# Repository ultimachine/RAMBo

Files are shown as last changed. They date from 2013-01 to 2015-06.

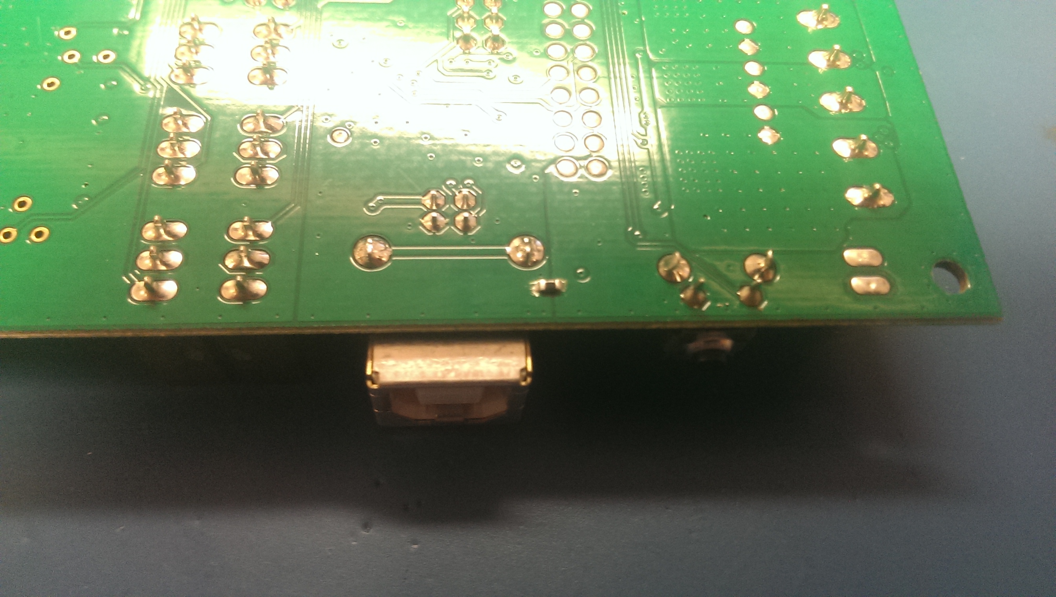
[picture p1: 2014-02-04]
docs/v1-2-ESD-patch/SMT-patch.jpg

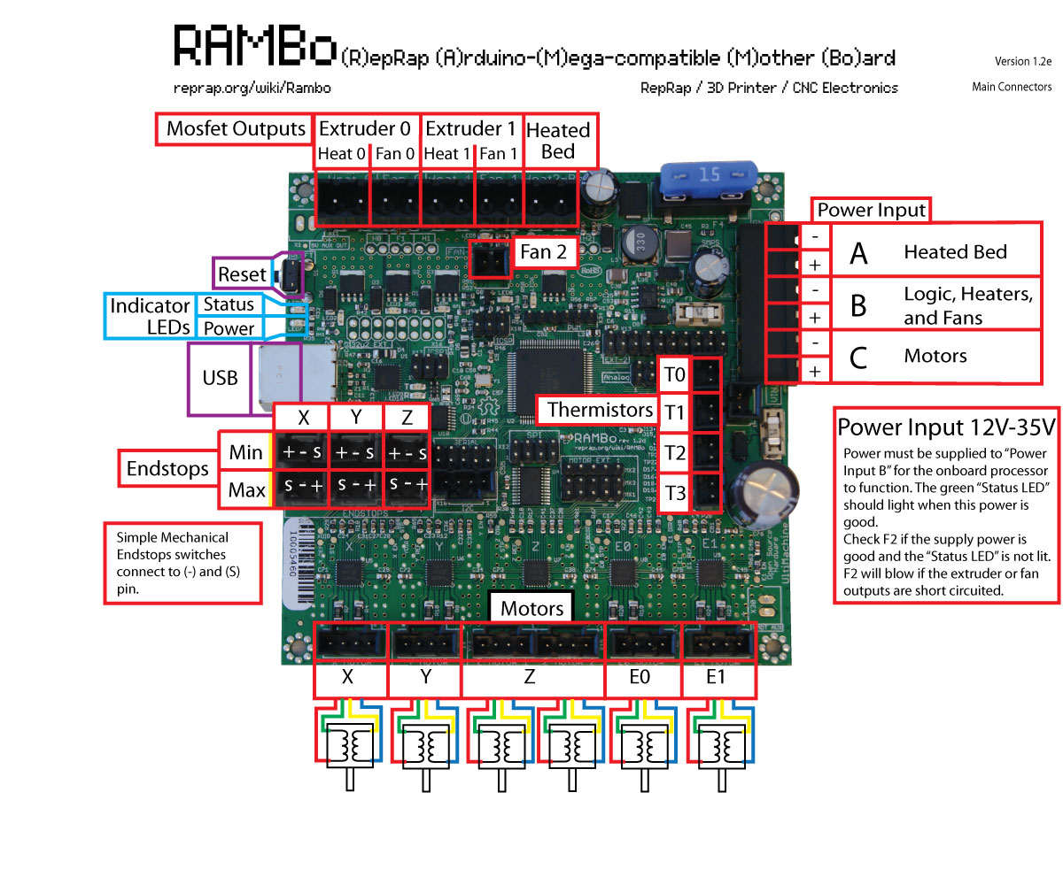
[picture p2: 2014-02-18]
docs/images/Rambo-conn-main.jpg

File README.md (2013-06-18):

RAMBo 3D Printer electronics
=====

This board is based off the Arduino MEGA design and work of RepRap community. It has 5 stepper drivers and 5 mosfet switched outputs.

There is no warantee for these files in any way. They are used to produce these boards, but there may have been some undocumented tweaks by various designers, engineers, manufacturers, suppliers, and assemblers to make this a functional product.

If you have any questions, suggestions, or comments please use the issues tracker at github.org/ultimachine/RAMBo/issues for now.

Please report bugs at github.org/ultimachine/RAMBo/issues

Documentation is at reprap.org/wiki/rambo

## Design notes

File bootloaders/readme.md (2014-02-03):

Use https://github.com/arduino/Arduino-stk500v2-bootloader for the Atmega2560 bootloader

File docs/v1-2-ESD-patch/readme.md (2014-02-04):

Applicable to RAMBo version 1.2

You should be able to get the patch from the vendor where you received the RAMBo.

The patch is a varistor between the USB ground and primary ground to provide a path for ESD to the USB shield.

The plug-in-patch uses part number VA100026D580DL between GND pins in ICSP1 and Serial extensions. If you are using the serial extension you can use GND in ICSP, I2C, or Z-MAX. The varistor should be completely covered in heat shrink tubing.

The SMT patch uses part CG0603MLC-05E.

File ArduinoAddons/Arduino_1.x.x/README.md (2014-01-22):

To access the extra pins in EXT-2 header:  

Install the arduino software IDE/toolset 1.x.x http://www.arduino.cc/en/Main/Software  

Current recommended is Arduino version 1.0.5
The rambo directory here needs to be copied to the arduino environment in the hardware folder. You should end with a boards.txt file at arduino-1.0.5/hardware/rambo/boards.txt

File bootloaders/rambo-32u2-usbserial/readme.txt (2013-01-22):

//this firmware and document modified from Arduino's source.
To setup the project and upload the RAMBo usbserial application firmware to an ATMEGA32U2 using the USB DFU bootloader:
1. unpack the source into LUFA's Projects directory
2. set ARDUINO_MODEL_PID in the makefile as appropriate
3. do "make clean; make"
4. put the 8U2 into USB DFU mode:
4.a. assert and hold the 8U2's RESET line
4.b. assert and hold the 8U2's HWB line
4.c. release the 8U2's RESET line
4.d. release the 8U2's HWB line
5. confirm that the board enumerates as either "Arduino Uno DFU" or "Arduino Mega 2560 DFU"
6. do "make dfu" (OS X or Linux - dfu-programmer must be installed first) or "make flip" (Windows - Flip must be installed first) or use the AVR Flip app.

Check that the board enumerates as either "RAMBo". You may also need to upload stk500v2 bootloader to the 2560 if it is not already. 
Test by uploading a new Arduino sketch from the Arduino IDE.

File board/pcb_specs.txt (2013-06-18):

4 layers, 0.062", FR4-TG170, 2oz, ENIG GOLD, GREEN SOLDER MASK, TWO SIDE MASK, WHITE SILK SCREEN, TOP SILK, Min Trace: 6mil, 4.05" x 4.10"11

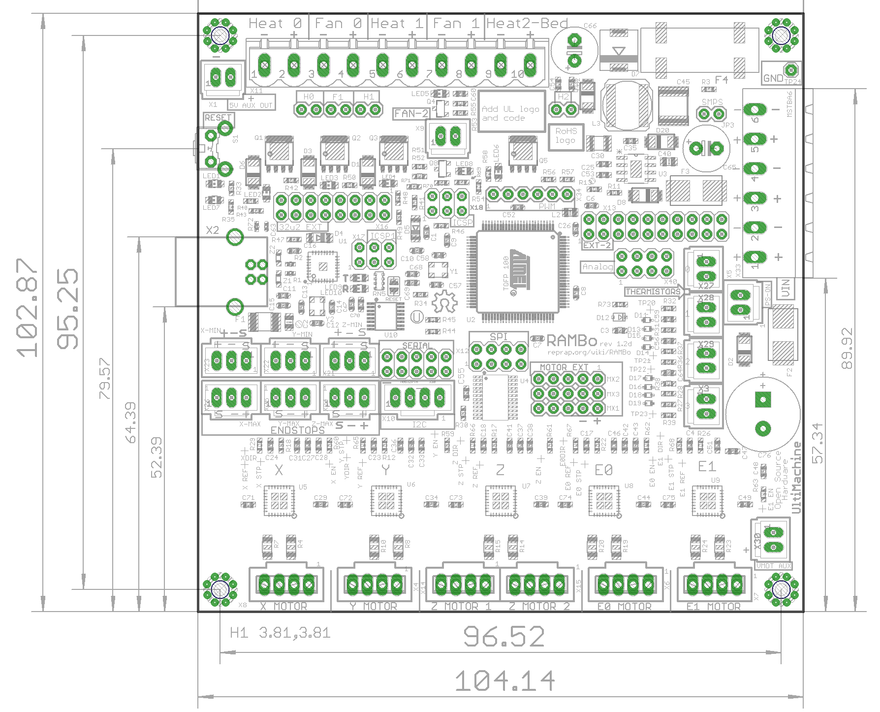
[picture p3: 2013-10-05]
docs/images/RAMBo-Silk.png

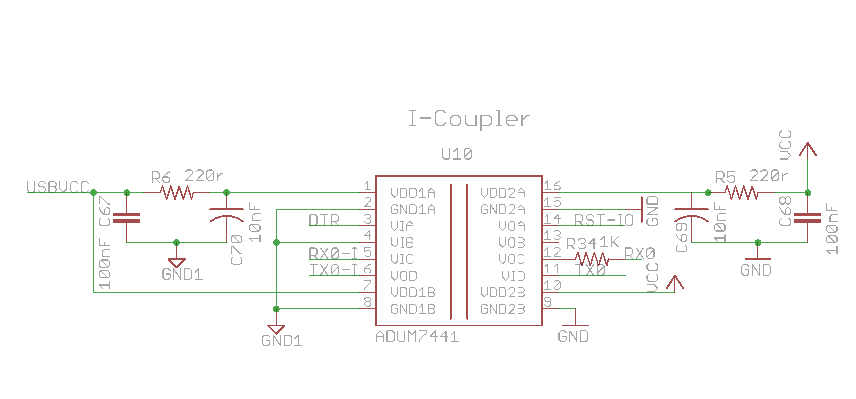
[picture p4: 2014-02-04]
docs/v1-2-ESD-patch/schem.png

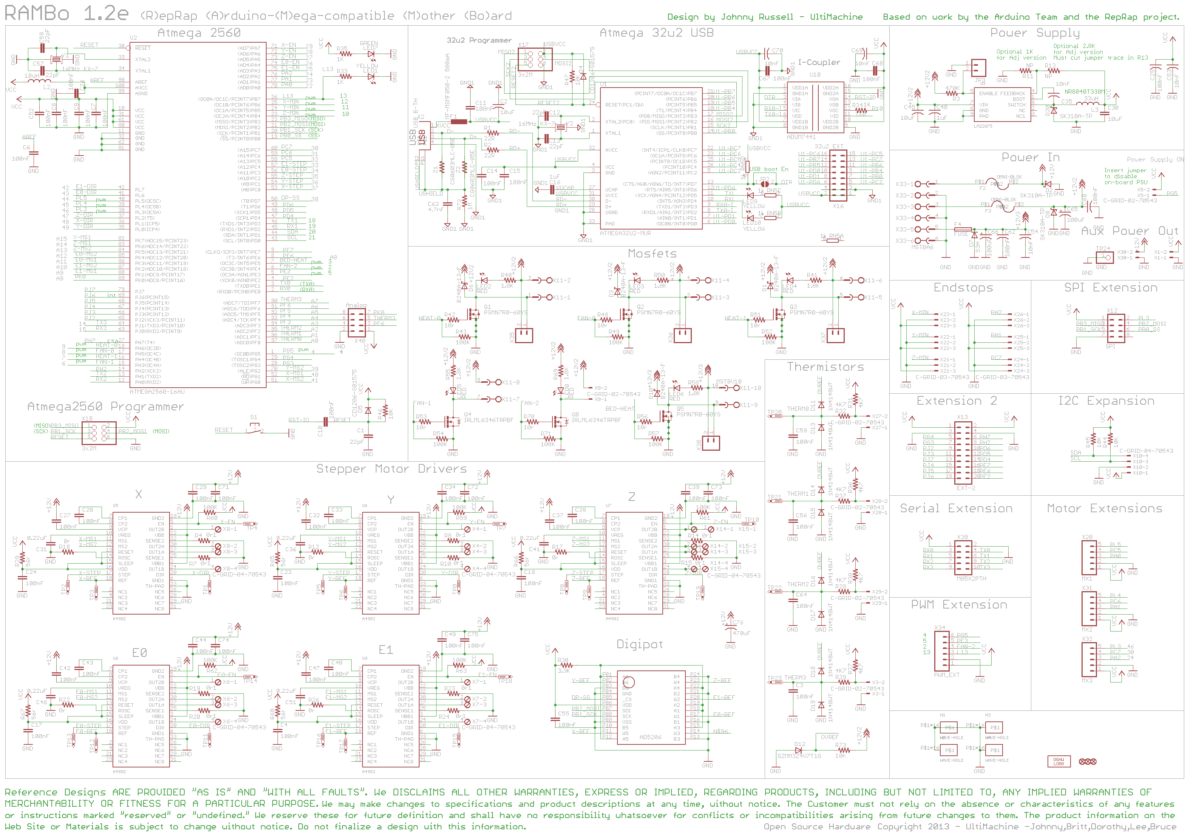
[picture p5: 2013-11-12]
docs/images/RAMBo-Schem.png

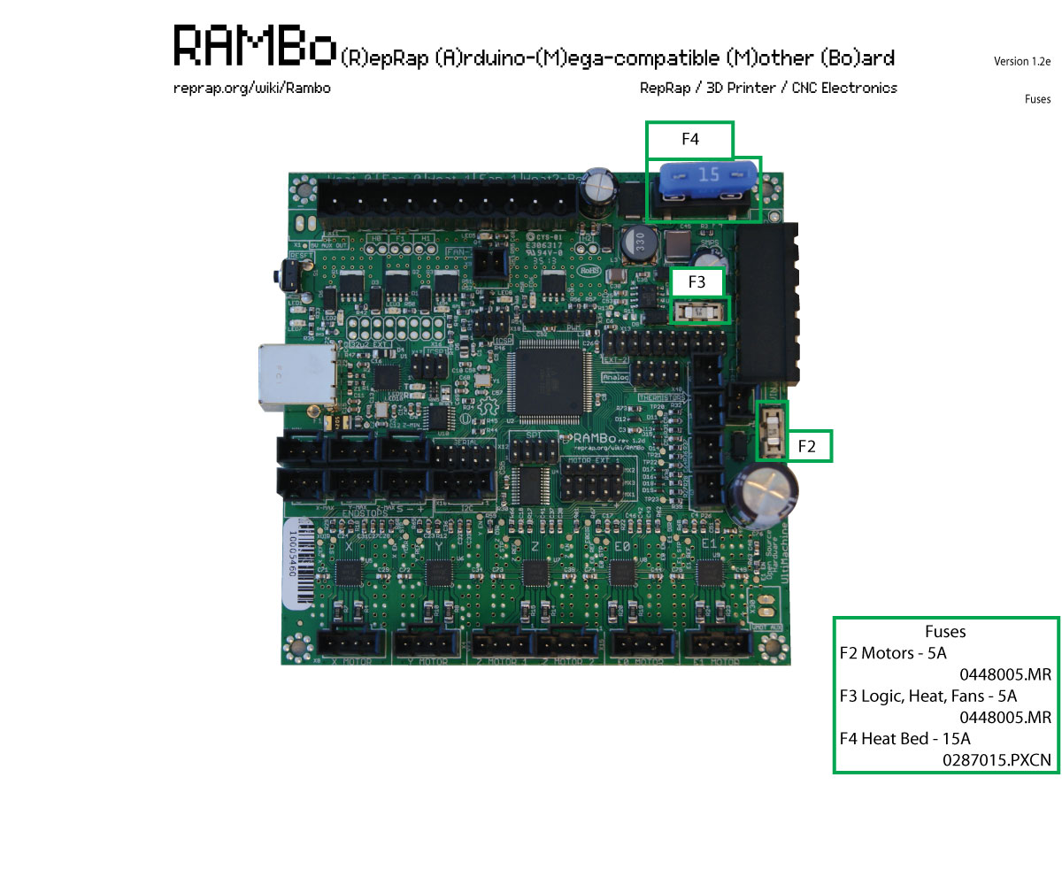
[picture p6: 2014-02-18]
docs/images/Rambo-fuses.jpg

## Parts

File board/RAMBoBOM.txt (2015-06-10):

Parts;Qty;Value;Device;Package;Description;Manufacturer;mfr  part #;;;
S1;1;;31-XX;B3F-31XX;SWITCH, TACTILE, SPST-NO, 50mA, THD ;Omron;1571610-2;;;
JP3, X35, X36, X37, X38;1;;M02PTH;1X02;1x2 header;;2211S-02G;;;
C31, C36, C41, C46, C51;5;0.22uF;C-EUC0603;C0603;0.22uF 100V capacitor X or 15%;Yageo;CC0603KRX7R7BB224 ;;;
R12, R17, R18, R22, R26;5;0r;R-US_R0603;R0603;0r (zero ohm) 100mW 5% resistor;Bourns;CR0603J000ELF;;;
R4, R7, R8, R10, R14, R15, R19, R20, R23, R24;10;0r1;R-US_R1206;R1206;0r1 (0.1ohm) .5mW 1% resistor;Bourns;CRM1206-FX-R100ELF;;;
R40, R41, R50, R55, R58, R69;6;1.8K;R-US_R0603;R0603;Resistor, Thick Film, 1.8K Ohm, 50V, 5±%, 100ppm, 0603 Case Size ;;RC0603JR-071K8L;;;
R43, R49, R52, R54, R57, R59, R60, R61, R62, R63, R71;11;100K;R-US_R0603;R0603;100Kohm 100mW 1% resistor;Yageo;RC0603FR-07100KL;;;
C6, C7, C8, C9, C10, C11, C14, C15, C26, C52, C3, C4, C17, C18, C23, C24, C27, C28, C29, C32, C33, C34, C37, C38, C39, C42, C43, C44, C47, C48, C49, C55, C56, C59, C64, C71, C72, C73, C74, C75, C25, C60, C62;43;100nF;C-EU0603-RND;C0603-ROUND;0.1uF 50V capacitor;Kemet;x16;;;
C65, C66;2;100uF;CPOL-USE3.5-8;E3,5-8;Aluminum Electrolytic Capacitors - Leaded 100uF 50V 20% 105c ;Nichicon;UVZ1H101MPD1TD;;;
R44, R45, R46, R47, R73;5;10K;R-US_R0603;R0603;10Kohm 100mW 1% resistor;Panasonic;ERJ-3EKF1002V;;;
C35, C53, C54;3;10nF;C-USC0603;C0603;10nF (0.01uF) 25V capacitor;TDK;C1608X7R1E103K080AA;;;
R42, R48, R51, R53, R56, R70;6;10r;R-US_R0603;R0603;10r (10ohm) 100mW 1% resistor;Vishay;CRCW060310R0FKEA;;;
C30;1;10uF;C-EUC1210K;C1210K;Multilayer Ceramic Capacitors MLCC - SMD/SMT 1210 10uF 25volts X5R 10% ;TDK;C3225X5R1E106K;;;
C2;1;10uF;C-USC0805;C0805;10uF;Kemet;C0805C106K8PACTU;;;
C45;1;10uF;C-USC2220K;C2220K;10uF;TDK;C5750X7R1H106M230KB;;;
Y1, Y2;2;16MHz KX-7;CRYSTAL-3.2-2.5;CRYSTAL-3.2-2.5;16MHz KX-7 10ppm crystal;TXC;7M-16.000MEEQ-T;;;
R33, R34, R35;3;1K;R-US_R0603;R0603;RESISTOR, THICK FILM, 1KOHM, 100mW, 1% ;Panasonic;ERJ-3EKF1001V;;;
R72;1;1M;R-US_R0402;R0402;RES 1M OHM 1/10W 5% 0402 SMD;Panasonic;ERJ2GEJ105X;;;
D11, D13, D14, D15, D16, D17, D18, D19;8;1N4148WT;1N4148WT;SOD523;Diode Small Signal Switching 75V 2-Pin SOD-523F T/R ;Fairchild;1N4148WT ;;;
RN5;1;1k;4R-NCAY16;CAY16;Resistor Networks & Arrays 1K 5% Convex 4resistors ;Bourns;CAY16-102J4LF;;;
C16;1;1uF;C-EU0603-RND;C0603-ROUND;1uF 10V capacitor;yageo;CC0603ZRY5V6BB105 ;;;
C40;1;1uF;C-USC0805;C0805;Multilayer Ceramic Capacitors MLCC - SMD/SMT 1.0UF 50V 10% 0805  ;Murata;GRM21BR71H105KA12L;;;
R1, R2;2;22R;R-US_R0402;R0402;22R (22ohm) 62.5mW 1% resistor;Yageo;RC0402FR-0722RL;;;
C1, C12, C13, C57, C58;5;22pF;C-EU0603-RND;C0603-ROUND;22pF 50V capacitor;TDK;C1608C0G1H220J;;;
R30;1;3.3K;R-US_R0603;R0603;RESISTOR, THICK FILM, 3.3KOHM, 100mW, 5% ;panasonic;erj3geyj332v;;;
X16;0;32u2 EXT;M08X2;2X8;2x8 header;;;;;
L3;1;33uH;L-USNR8040;NR8040;Fixed Inductors 33uH;TDK;VLP8040T-330M;;;
X17, X18;2;3x2M;PINHD-2X3;2X03;2x3 header;;2213S-06G;;;
C63;1;4.7nF;C-EUC0402;C0402;Multilayer Ceramic Capacitors MLCC - SMD/SMT 4.7nF 25V X7R 10% ;;CC0402KRX7R8BB472;;;
R3;1;470K;R-US_R0603;R0603;SMD 1/10watt 470Kohms 1% Thick Film Resistors;Vishay;CRCW0603470KFKEA ;;;
C76;1;470uF;CPOL-USC12,5-5;C12,5-5;CAPACITOR ALUM ELEC, 470UF, 50V, 20%, RADIAL;nichicon;UPW1H471MHD1TO;;;
;0;;;;Alternate capacitor;;UVZ1H471MHD1TO;;;
R27, R28, R31, R32, R36, R37, R38, R39;8;4K7;R-US_R0603;R0603;4K7 (4.7Kohm) 100mW 1% resistor;Panasonic;ERJ3EKF4701V;;;
R29, R65, R66, R67, R68;5;56r;R-US_R0603;R0603;RESISTOR, THICK FILM, 56OHM, 100mW, 5% ;Vishay;CRCW060356R0JNEA;Till 05/22/2014;200bds w/drivers;
U5, U6, U7, U8, U9;5;A4982;A4982QFN32ROUNDPADS;QFN32TROUND;A4982;Allegro;A4982SETTR-T;2100;6500;325
U4;1;AD5206;AD5206;TSSOP24;AD5206 (IC);Analog Devices;AD5206BRUZ10-RL7;;currently 300bd/wk;
U10;1;ADUM7441;ADUM7441;QSOP16;ADUM7441;Analog Devices;ADUM7441ARQZ-RL7;;;
U2;1;ATMEGA2560-16AU;ATMEGA25602560-16AU;TQFP100;ATMEGA2560-16AU (IC);Atmel;ATMEGA2560-16AUR;;;
U1;1;ATMEGA32U2-MUR;ATMEGA16U2-MU;MLF32;ATMEGA32U2-MUR (IC);Atmel;ATMEGA32U2MU;;;
D1, D3, D6, D10;7;B240A-13-F;SCHOTTKY-DIODE;SMA-SM;3.0A 100V Diode;Diodes Inc.;SK310A-TP;;;
X1, X3, X5, X9, X27, X28, X29, X30;6;C-GRID-02-70543;C-GRID-02-70543;70543-02;WIRE-BOARD CONNECTOR HEADER 2POS, 2.54MM ;Molex;70543-0001;;;
X21, X22, X23, X24, X25, X26;6;C-GRID-03-70543;C-GRID-03-70543;70543-03;WIRE-BOARD CONNECTOR HEADER 3POS, 2.54MM ;Molex;70543-0002;;;
X4, X6, X7, X8, X10, X14, X15;7;C-GRID-04-70543;MPT4;4POL254;WIRE-BOARD CONNECTOR HEADER 4POS, 2.54MM ;Molex;70543-0038;;;
L2;1;10uH;L-US;C0805;INDUCTOR 10UH 20% 0805 SMD;Taiyo Yuden;CBC2012T100M;;;
D4, D5;2;CD1206-S01575;DIODE-MINIMELF;MINIMELF;100V 150mA diode;Bourns;CD1206-S01575;;;
Z1, Z2;2;CG0603MLC-05E;VARISTORCN0603;CT/CN0603;5V 20V varistor;Bourns;CG0603MLC-05E;;;
X13;1;EXT-2;M10X2;2X10;2x10 header;;2213S-20G ;;;
F4;1;FUSE;FUSE;FUSE-ATO-SMD;FUSE HOLDER, AUTO BLADE, SMT ;Keystone;3587TR;;;
D40;1;RSB39VTE-17;PINHD-1X1;SOD323;TVS DIODE 30VWM SOD323;;RSB39VTE-17;;;
D9, D21, D22, D23, D24, D25, D26, D27, D28, D29, D30, D31, D32, D33, D34, D35, D36, D37, D38, D39;20;GND;PINHD-1X1;1X01;TVS DIODE 30VWM SMD ;;SMAJ30A;;;
C67, C68, C69, C70;4;100nF;C-EU0603-RND;C0402;CAP CER 0.1UF 16V 10% X7R 0402 ;;GRM155R71C104KA88D ;;;
LED7;1;GREEN;LEDCHIP-LED0805;CHIP-LED0805;GREEN LED;;598-8170-107F ;;;
Q4, Q8;2;IRLML6346TRPBF;MOSFET-NCHANNELSMD;SOT23-3;N CH MOSFET, 30V, 3.4A, 3-SOT-23;;IRLML6346TRPBF;;;
U3;1;LM22675;LM22675;SOIC127P600X170-9N;IC REG BUCK 5V 1A 8SOPWRPAD;;LM22675;;;
X20;1;M05PTH;M05PTH;1X05;1x5;;2211S-05G;;;
X39, X32;2;M05X2PTH;M05X2PTH;AVR_ICSP;2x5 header;;2213S-10G;;;
F1;1;MF-MSMF050-2 500mA;L-EUL1812;L1812;500mA 15V fuse ptc reset;Bourns;MF-MSMF050-2;;;
X33;1;MSTBA6;MSTBA6;MSTBA6;6 pin fixed terminal block;Molex;39532-1006;;;
X11;1;MSTBV10;MSTBV10;MSTBV10;CONN HEADER 10POS 5.08MM STR TIN;Molex;395311010;;;
R11, R13;0;NP;R-US_R0603;R0603;;;;;;
F2, F3;2;OMNI-BLOK;OMNI-BLOK;OMNI-BLOK;5A fuse/fuse block;Littlefuse;0154005.DR;;;
Q1, Q2, Q3, Q5;4;PSMN7R0-60YS;PH7030L;SOT669;PH7030L (Mosfet) 60V 356A 117W;NXP;PSMN7R0-60YS,115;;;
X34;1;PWM_EXT;M06SIP;1X06;1x6 header;;2213S-06G;;;
LED2, LED3, LED4, LED5, LED6, LED8;6;RED;LEDCHIP-LED0805;CHIP-LED0805;RED;Dialight;5988110107F ;;;
D7;1;S3A;DIODE-D0-214AB;DO-214AB;3A 50V Diode;;S3A;;;
X12, X40;2;SPI;M04X2;2X4;M04X2;;2213S-08G ;;;
D12;1;SZMM3Z4V7T1G;ZENER-DIODESOD323;SOD323-R;Zener Diodes ZEN REG 0.2W 4.7V;;SZMM3Z4V7T1G;;;
X2;1;USB B-TH;PN61729;PN61729;USB B-TH connector;FCI;61729-0010BLF;;;
LED1, LED9, LED10;3;YELLOW;LEDCHIP-LED0805;CHIP-LED0805;YELLOW LED;Dialight;    5988140107F;;;
CF1, CF2, CF3, CF4, CF5, CF6, CF7, CF8, CF9, CF10, CF11, CF12, CF13, CF14, CF15, CF16, CF17, CF18, CF19, CF20;20;;;;EMI Filter 2A 50VDC Flat Style SMD;;NFM21CC223R1H3D;;;
L1, L4;2;;;;FERRITE CHIP 60 OHM 6000MA 1806 ;;BLM41PG600SN1L;;;
D9, D21, D22, D23, D24, D25, D26, D27, D28, D29, D30, D31, D32, D33, D34, D35, D36, D37, D38, D39;20;;;;TVS DIODE 30VWM 48.4VC SMA ;;SMAJ30A;;;
;;;;;;;;;;
PCB;1;;;;PCB;UltiMachine;UMRAMBOPCB1.3L;;;
;;;;;;;;;;
White Wire;0.012;;;;white wire;;1853 WH001;;;
Black Wire;0.008;;;;black wire;;1853 BK001;;;
loose gold connectors;34;;;;CONTACT, FEMALE, 30-24AWG, CRIMP ;molex;16-02-0097;;;
replacement fuses;0;;;;;;0448005.MR;;;
2pos 5.08mm Pluggable;5;;;;TERMINAL BLOCK, PLUGGABLE, 2 POS, 24-12AWG ;Molex;39530-0002;;;
6pos 5.08mm Pluggable;1;;;;TERMINAL BLOCK PLUGGABLE, 6POS, 24-12AWG ;Molex;39530-0006;;;
gold crimp on reel;10;;;;GOLD CONTACT, FEMALE, 30-24AWG, CRIMP ;Molex;16020082;;;
15A ATO fuse;1;;;;ATO fuse 15A;Littelfuse;0287015.PXCN;;;
4P POSITIVE LATCH;6;;;;WIRE-BOARD CONNECTOR RECEPTACLE, 4POS, 2.54MM ;Molex;50-57-9404;;;
3P POSITIVE LATCH;3;;;;WIRE-BOARD CONNECTOR RECEPTACLE, 3POS, 2.54MM ;Molex;50-57-9403;;;
2P POSITIVE LATCH;3;;;;WIRE-BOARD CONNECTOR RECEPTACLE, 2POS, 2.54MM ;Molex;50-57-9402;;;
ULTRA-FAST RECEPT;6;;;;TERMINAL FEMALE DISCONNECT 3.18MM VIOLET;TE;7-520366-2;;;
microswitches;3;;;;microswitches;Omron;SS-3GL13PT;;;
microswitches;0;;;;microswitch  flat;Omron;SS-3GLPT ;;;
USB A-B cable;1;;;;USB A-B cable;;;;;
X11;0;MSTBV10;MSTBV10;MSTBV10;TERMINAL BLOCK EUROSTYLE 10POS, 26-14AWG;multicomp;MB612-50810;;;

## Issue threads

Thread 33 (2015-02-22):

ATX PSU 5v Standby Pin

avluis, 2015-02-22:
Since the change from 1.1 to 1.2, the logic is powered by 12v from the power supply right?
Are we able to cut a trace on 1.2 and newer to supply 5v standby power to be able to use an ATX PSU's 5v standby and PS_ON pin with the corresponding ON - OFF G-code?

avluis, 2015-03-28:
After plenty of experimenting, I was able to figure out that I just need to supply 5V to one of the pins while the other is controlled by the firmware's M80 & M81 commands - just what I needed.
When looking at the RAMBo and the PS_ON header - the pin closer to the power supply input is the 5V pin.
A good way to test is to simply power the RAMBo as usual then send a few M80 & M81 commands while testing the open pin. You know you have the right pin when you see a ground signal.

Also, depending on the 5v power supply or just on the way your power supply is wired, you will need to have a diode on the 5v signal from your power supply.

Tailslide, 2017-10-24:
Can someone please explain how to do this in more detail?  The 5V standby power goes to the pin closest to the power supply input and the PS_ON goes to the other pin?  Where does the diode go and which way?

Closed 2015-03-28.

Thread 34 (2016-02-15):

Can't use PS_ON pin because logic has no power

levlandau, 2016-02-15:
I am trying to setup Rambo to turn on/ff the 24V power supply after the printing is done. [This guide](http://www.instructables.com/id/Converting-12v24v-power-supply-to-remote-G-code-sw/?ALLSTEPS) steps through how to do this with a relay.

I have Rambo rev 1.2h. It seems once the USB and logic 5V power were isolated, the logic no longer has power once the PSU is turned off. So it can't be used to turn the PSU on/off. The 5V pin next to the  PS_ON pin also has no power.

I have searched for documentation on how to resolve this problem, but there is nothing obvious. Rev 1.2h no longer has the jumper which allows one to select USB power for the logic side of the board.

Can someone explain how the PSU can be turned on/off correctly? Do I need to supply external 5V power as is suggested by [issue #33](https://github.com/ultimachine/RAMBo/issues/33) ??

tonokip, 2016-02-16:
Yes, you need to power logic independently in order to control the power supply.

The solution of using external 5V power and a diode seems like a good one.

Next to the bed fuse are 2 unpopulated pins labeled SMPS which you can use to disable the onboard 5V power supply. You can do this by soldering the two points together. This would allow you to use only the 5V external power to power the logic.

Other then that, the process of controlling the PSU is the same.

Tailslide, 2017-10-24:
Can someone please explain how to do this in more detail?  The 5V standby power goes to the pin closest to the power supply input and the PS_ON goes to the other pin?  Where does the diode go and which way?

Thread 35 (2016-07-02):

32 microsteps?

KissmanCZ, 2016-07-02:
What about use better motor drivers with 32 microsteps... is this possible in future versions of Rambo?

tonokip, 2017-10-23:
UltiMachine sells the Archim 1.0 with 32 microstepping drv8825 drivers and the Atmel sam3x8e (same as Arduino Due) processor.

Unless you look closely you could easily mistake it for a Rambo as it has the same dimensions and most of the same connector layout.

KissmanCZ, 2017-10-23:
lol... one year later? :) today I am using Einsy Rambo with Trinamic 2130 with 256 microsteps drivers ;)

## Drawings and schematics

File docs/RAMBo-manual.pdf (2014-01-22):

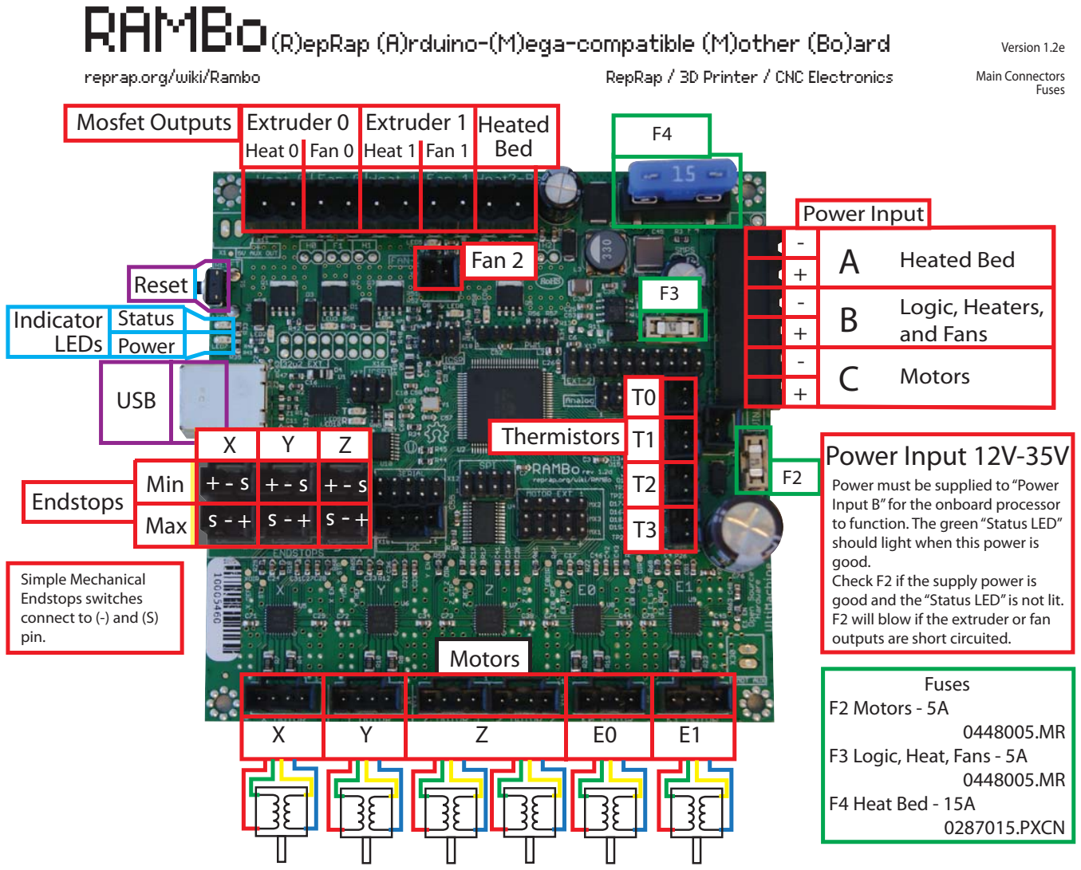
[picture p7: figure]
Fuses F2 Motors - 5A; 0448005.MR F3 Logic, Heat, Fans - 5A 0448005.MR F4 Heat Bed - 15A 0287015.PXCN; Fuses; Indicator LEDs; Status Power; Reset; USB; A Heated Bed; C Motors; Logic, Heaters, B and Fans; Power Input; Power must be supplied to “Power Input B” for the onboard processor to function. The green “Status LED” should light when this power is good. Check F2 if the supply power is good and the “Status LED” is not lit. F2 will blow if the extruder or fan outputs are short circuited.; Power Input 12V-35V; Mosfet Outputs; Extruder 0; Extruder 1; Fan 2; Heated; Heat 0; Fan 0; Heat 1; Fan 1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

Open Source Hardware | Copyright 2013 - UltiMachine -Johnny,Britt,Dorothy,Lee, Bruce

Handle with care. Static Sensitive device.

!!! Reversing input power can destroy electronics and cause fire hazard!!!

Test all electronics thoroughly before placing into service.

Do not leave power supplied to electronics unattended, or run machines unattended due to the risk of fire and malfunction.

This is NOT a toy and it contains small and sharp parts. Children can choke or suffocate by swallowing small objects. Keep all parts away from children and never leave printer/parts unattended.

reprap.org/wiki/Rambo | RepRap / 3D Printer / CNC Electronics

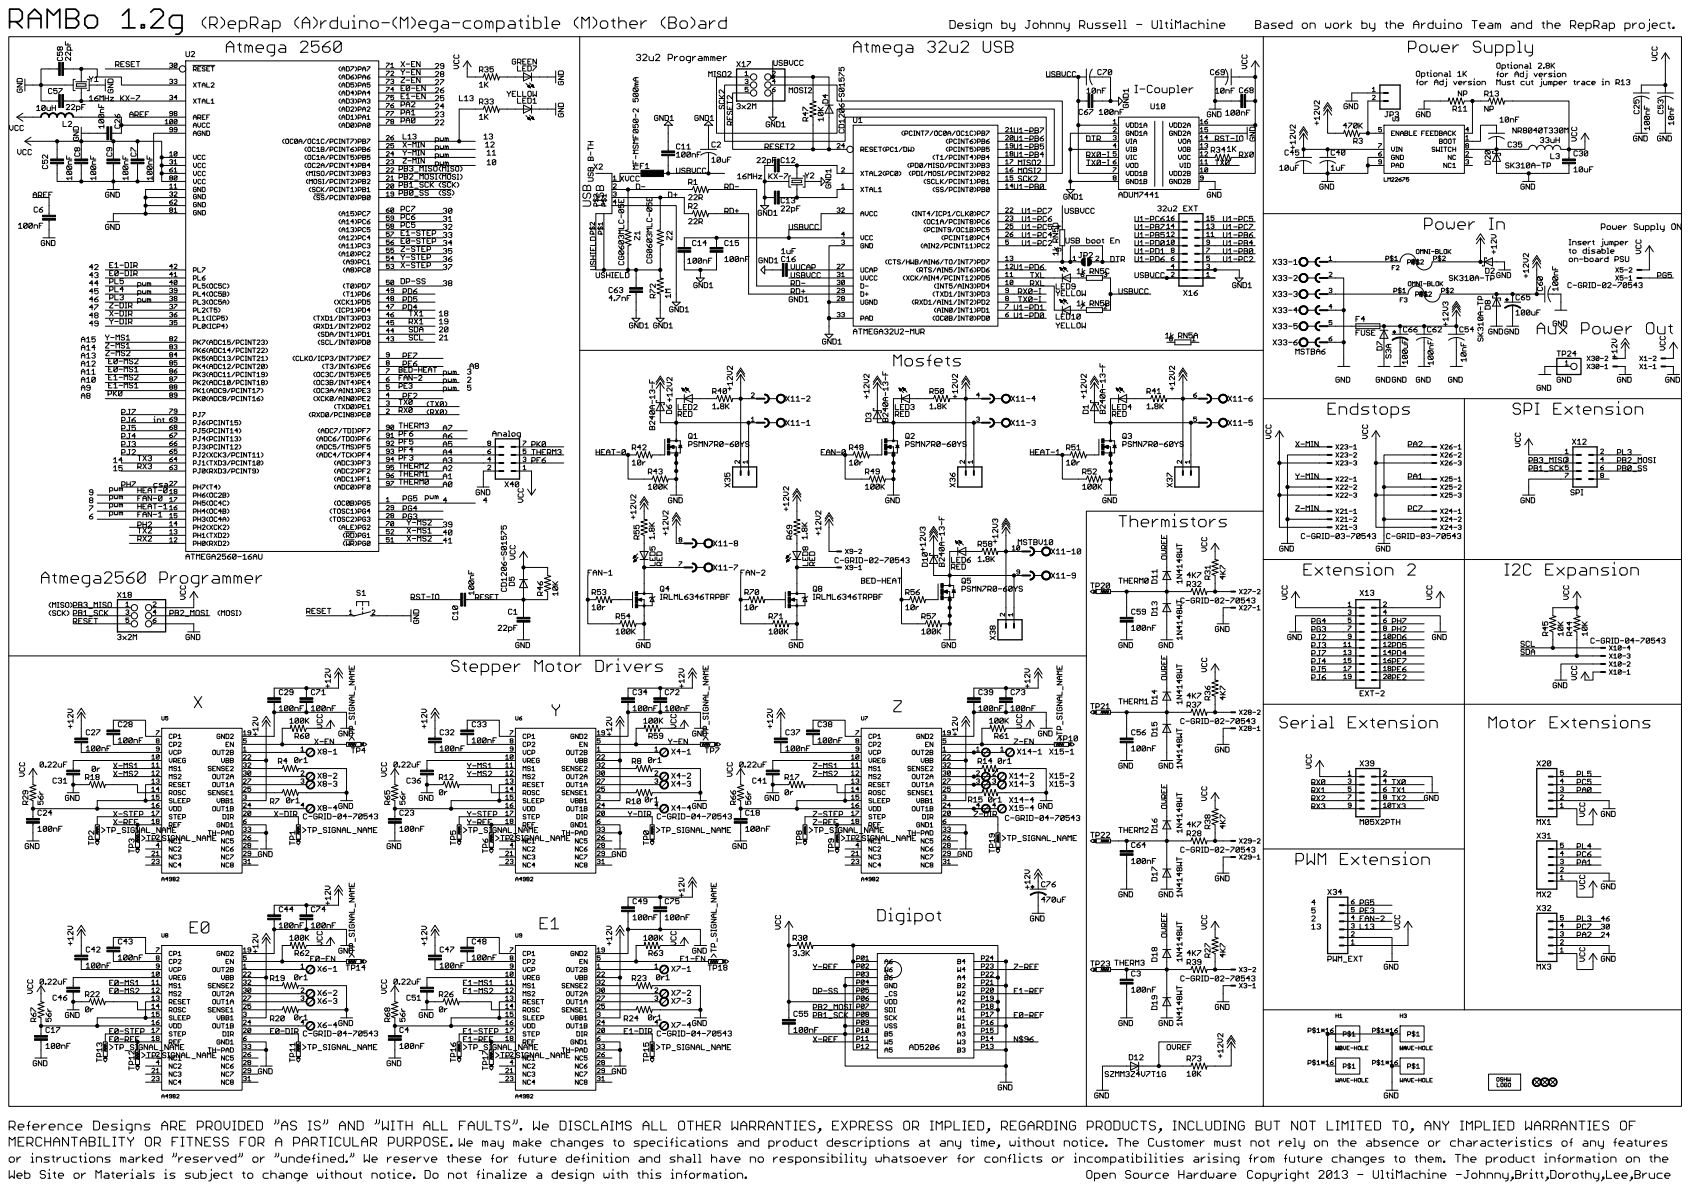
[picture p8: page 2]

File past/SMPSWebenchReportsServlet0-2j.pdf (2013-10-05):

## WEBENCH ® Design Report

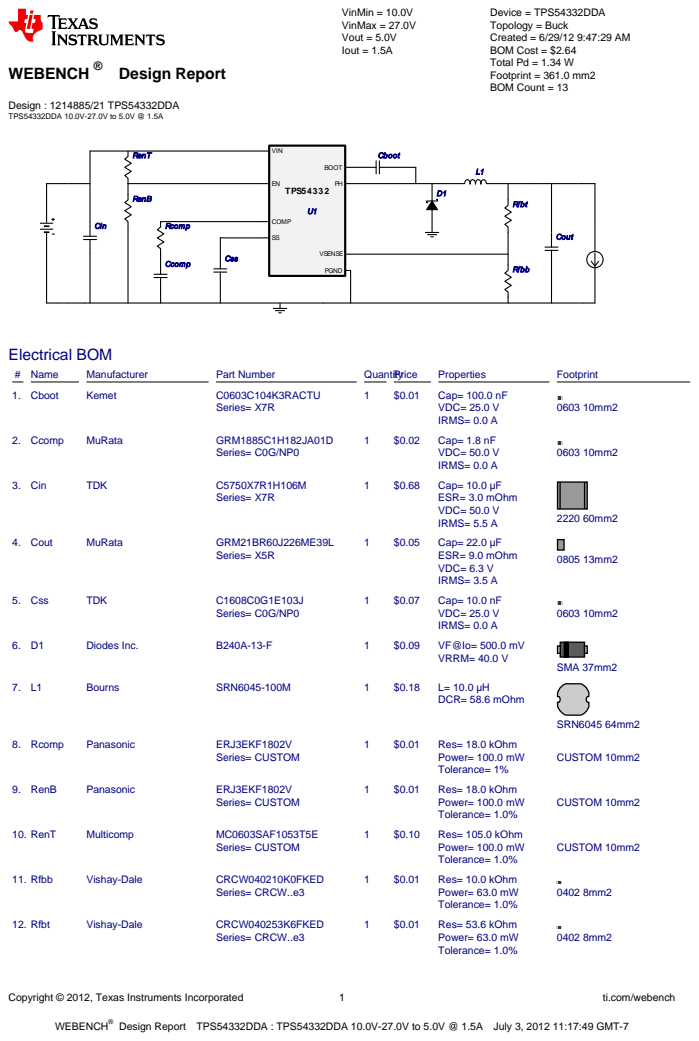
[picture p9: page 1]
Copyright © 2012, Texas Instruments Incorporated; ti.com/webench; WEBENCH®; Design : 1214885/21 TPS54332DDA TPS54332DDA 10.0V-27.0V to 5.0V @ 1.5A; VinMin = 10.0V VinMax = 27.0V Vout = 5.0V Iout = 1.5A; Device = TPS54332DDA Topology = Buck Created = 6/29/12 9:47:29 AM BOM Cost = $2.64 Total Pd = 1.34 W Footprint = 361.0 mm2 BOM Count = 13; Cboot; Ccomp; Cin; Cout; Css; Rcomp; RenB; RenT; Rfbb; Rfbt; TPS54332; VIN; COMP; BOOT; VSENSE; PGND; Electrical BOM; # Name; Manufacturer; Part Number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

Design Report TPS54332DDA : TPS54332DDA 10.0V-27.0V to 5.0V @ 1.5A July 3, 2012 11:17:49 GMT-7

WEBENCH®
Design
Copyright © 2012, Texas Instruments Incorporated | 2 | ti.com/webench

WEBENCH®
Design Report TPS54332DDA : TPS54332DDA 10.0V-27.0V to 5.0V @ 1.5A July 3, 2012 11:17:49 GMT-7
# Name | Manufacturer | Part Number | QuantityPrice | Properties | Footprint

13. U1 | Texas Instruments | TPS54332DDA (http://www.ti.com/product/tps54332) | 1 | $1.40 | Switcher
MPDS092E 57mm2

## Operating Values

# | Name | Value | Category | Description

1. BOM Count | 13.0 | Total Design BOM count
2. Total BOM | $2.641 | Total BOM Cost
3. Cin IRMS | 461.896 m A | Current | Input capacitor RMS ripple current
4. Cout IRMS | 127.31 m A | Current | Output capacitor RMS ripple current
5. IC Ipk | 1.721 A | Current | Peak switch current in IC
6. Iin Avg | 327.57 m A | Current | Average input current
7. L Ipp | 441.015 m A | Current | Peak-to-peak inductor ripple current
8. M1 Irms | 671.593 m A | Current | Q Iavg
9. FootPrint | 361.0 mm2 | General | Total Foot Print Area of BOM components
10. Frequency | 1000.0 k Hz | General | Switching frequency
11. IC Tolerance | 28.0 m V | General | IC Feedback Tolerance
12. M Vds Act | 63.268 m V | General | Voltage drop across the MosFET
13. Mode | CCM | General | Conduction Mode
14. Pout | 7.5 W | General | Total output power
15. D1 Tj | 44.991 degC | Op_Point | D1 junction temperature
16. Vout OP | 5.0 V | Op_Point | Operational Output Voltage
17. Cross Freq | 61.073 k Hz | Op_point | Bode plot crossover frequency
18. Duty Cycle | 20.046 % | Op_point | Duty cycle
19. Efficiency | 84.799 % | Op_point | Steady state efficiency
20. IC Tj | 59.948 degC | Op_point | IC junction temperature
21. ICThetaJA | 50.0 degC/W | Op_point | IC junction-to-ambient thermal resistance
22. IOUT_OP | 1.5 A | Op_point | Iout operating point
23. Phase Marg | 101.888 deg | Op_point | Bode Plot Phase Margin
24. VIN_OP | 27.0 V | Op_point | Vin operating point
25. Vout p-p | 7.783 m V | Op_point | Peak-to-peak output ripple voltage
26. Cin Pd | 640.043 µ W | Power | Input capacitor power dissipation
27. Cout Pd | 145.87 µ W | Power | Output capacitor power dissipation
28. Diode Pd | 599.654 m W | Power | Diode power dissipation
29. IC Pd | 598.96 m W | Power | IC power dissipation
30. L Pd | 145.035 m W | Power | Inductor power dissipation
31. Total Pd | 1.344 W | Power | Total Power Dissipation

## Design Inputs

# | Name | Value | Description

1. Iout | 1.5 A | Maximum Output Current
2. Iout1 | 1.5 Amps | Output Current #1
3. VinMax | 27.0 V | Maximum input voltage
4. VinMin | 10.0 V | Minimum input voltage
5. Vout | 5.0 V | Output Voltage
6. Vout1 | 5.0 Volt | Output Voltage #1
7. base_pn | TPS54332 | Texas Instruments base part number
8. Ta | 30.0 degC | Ambient temperature

## Design Assistance
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

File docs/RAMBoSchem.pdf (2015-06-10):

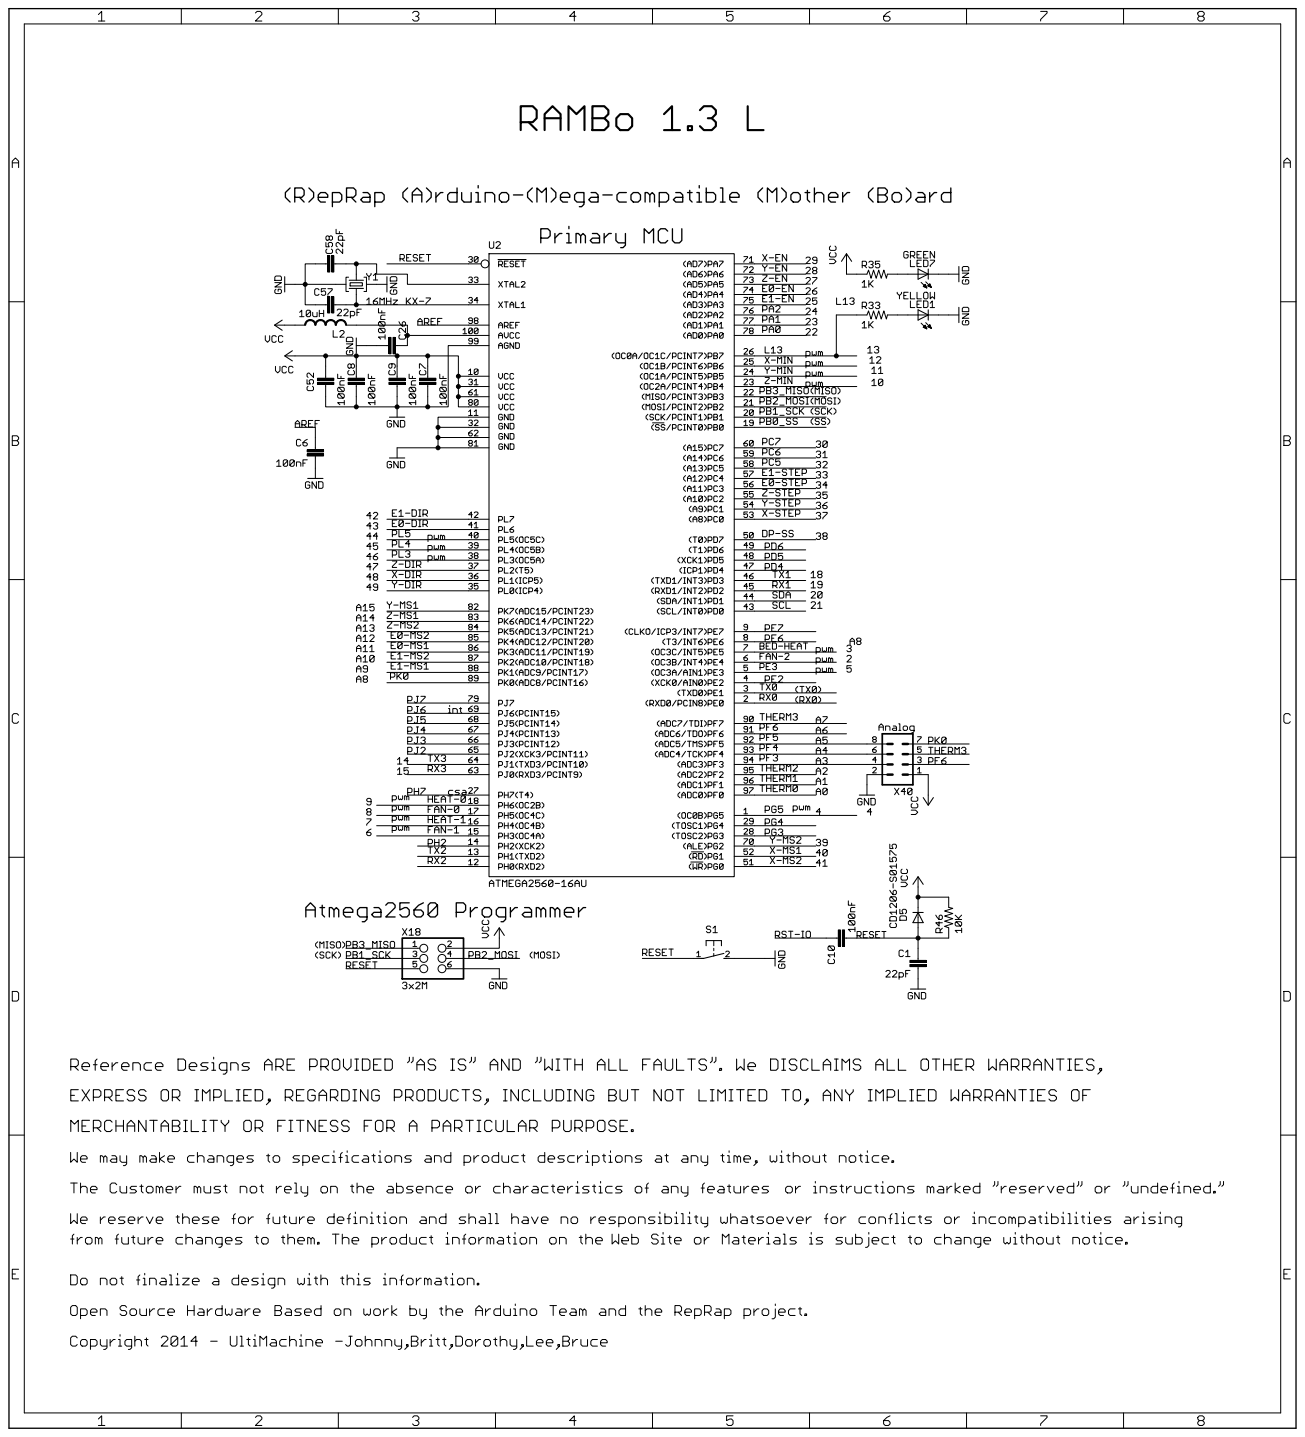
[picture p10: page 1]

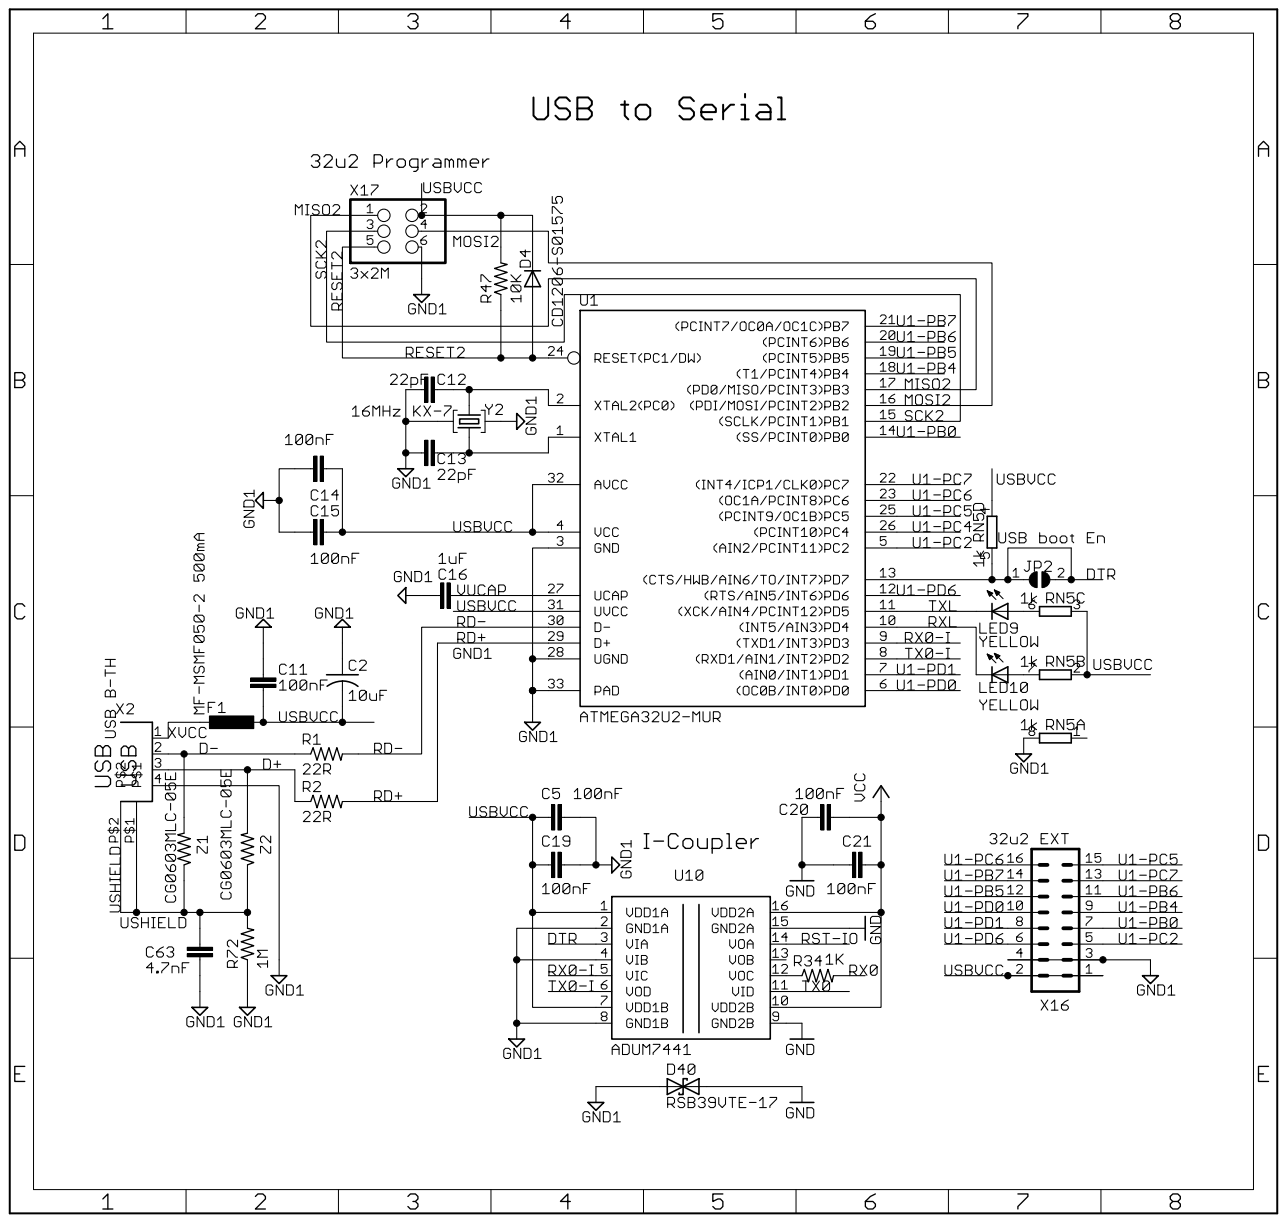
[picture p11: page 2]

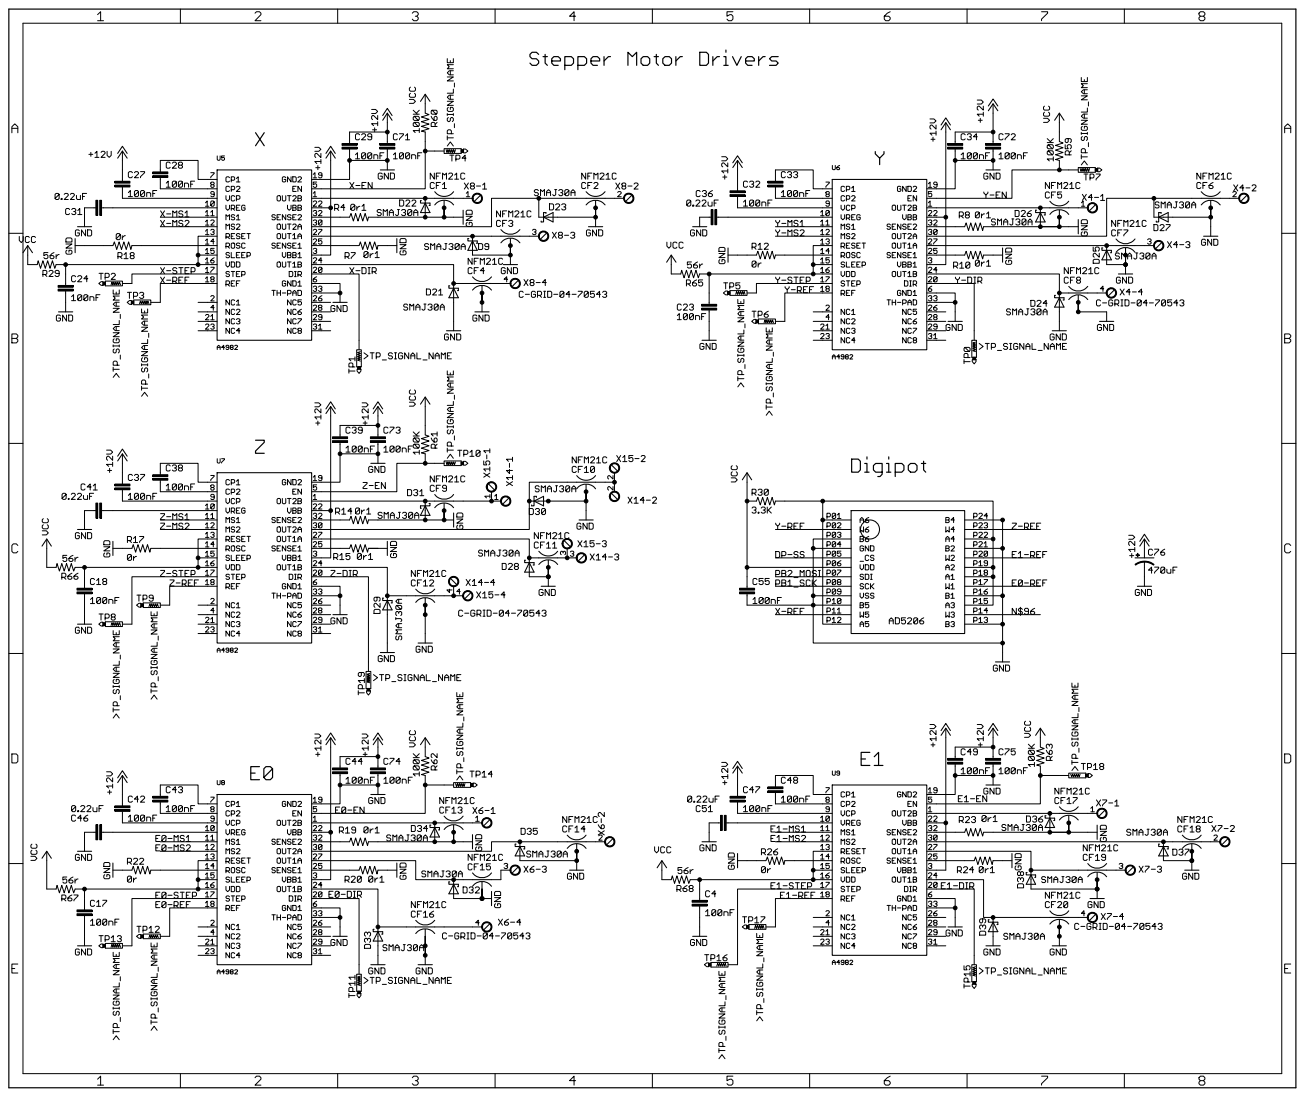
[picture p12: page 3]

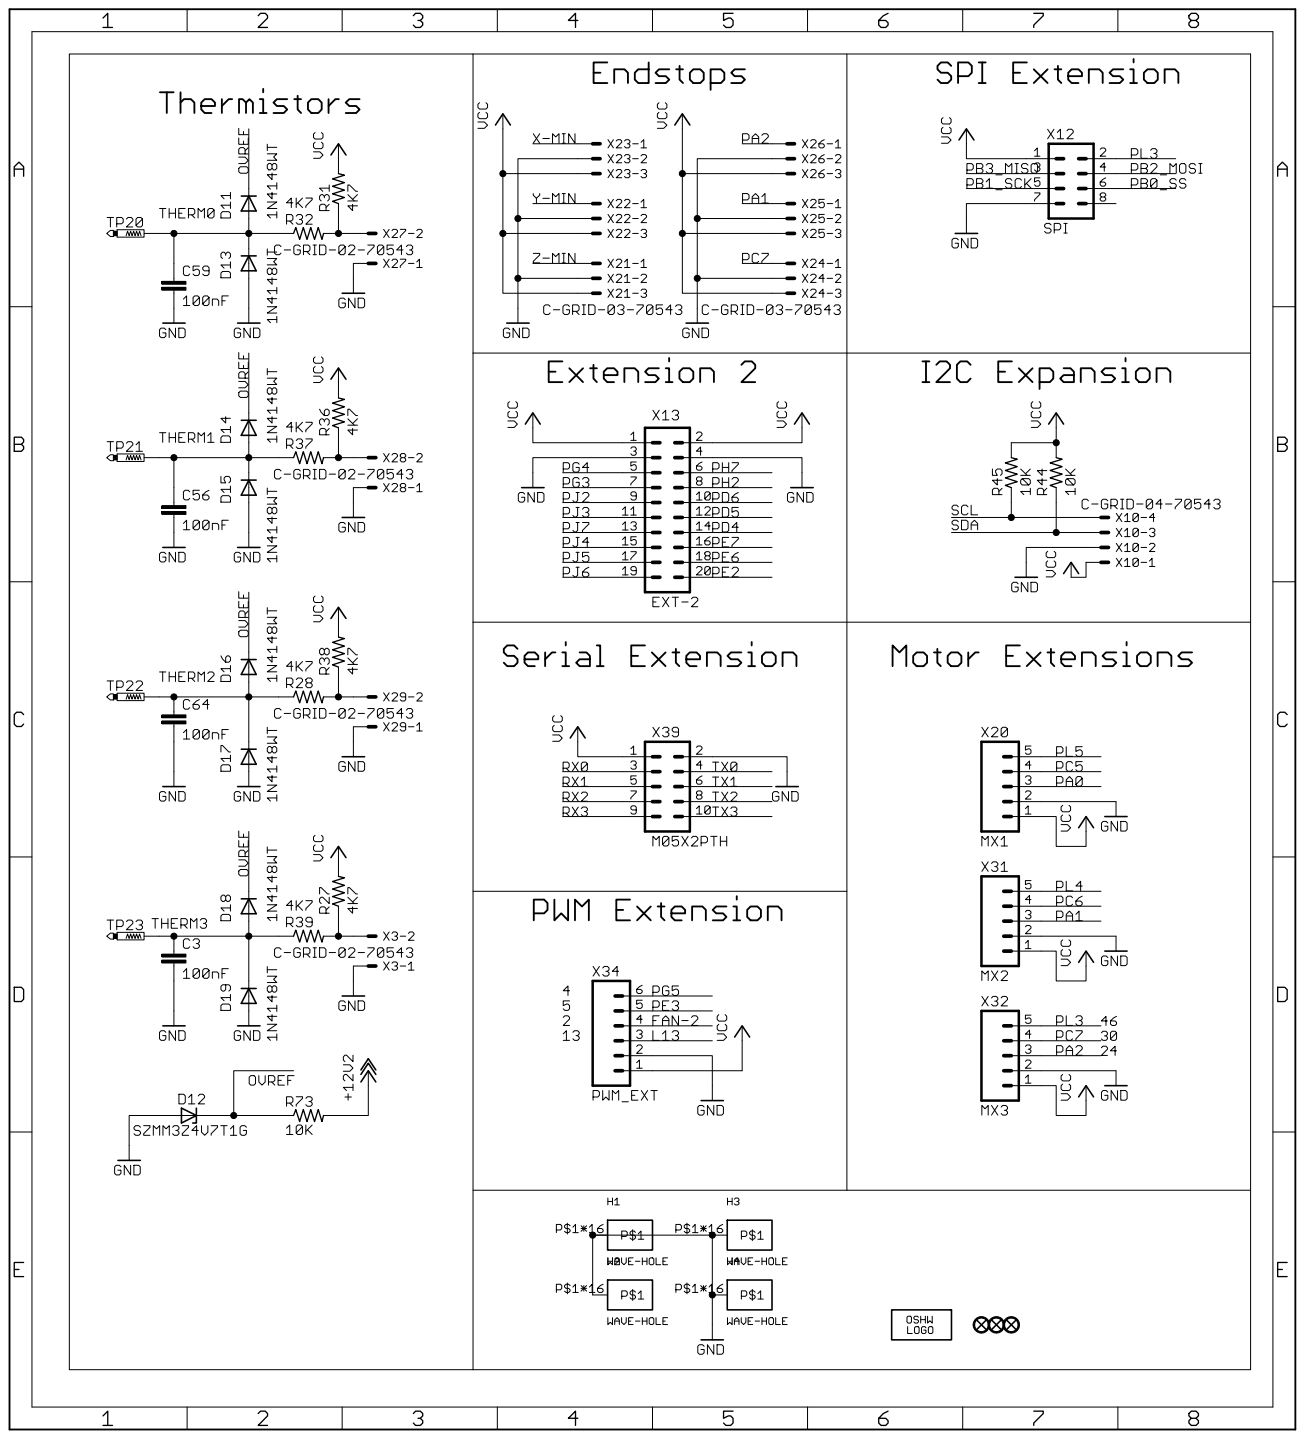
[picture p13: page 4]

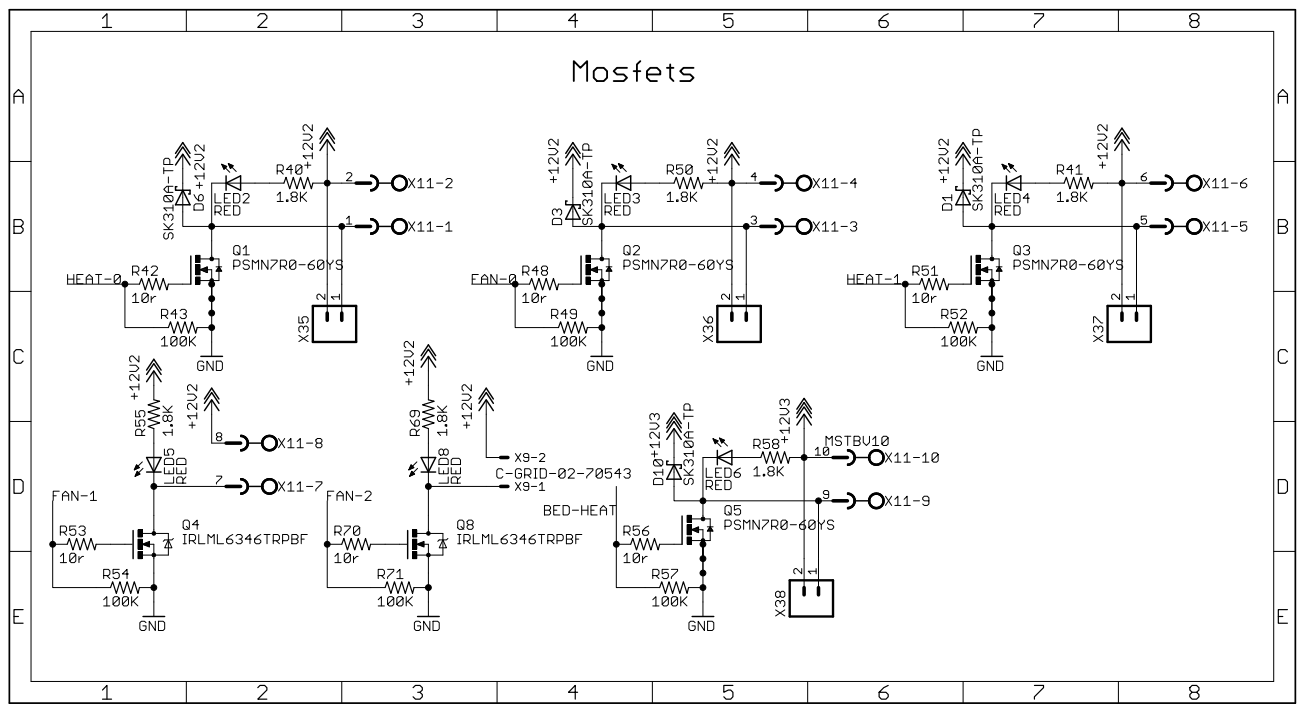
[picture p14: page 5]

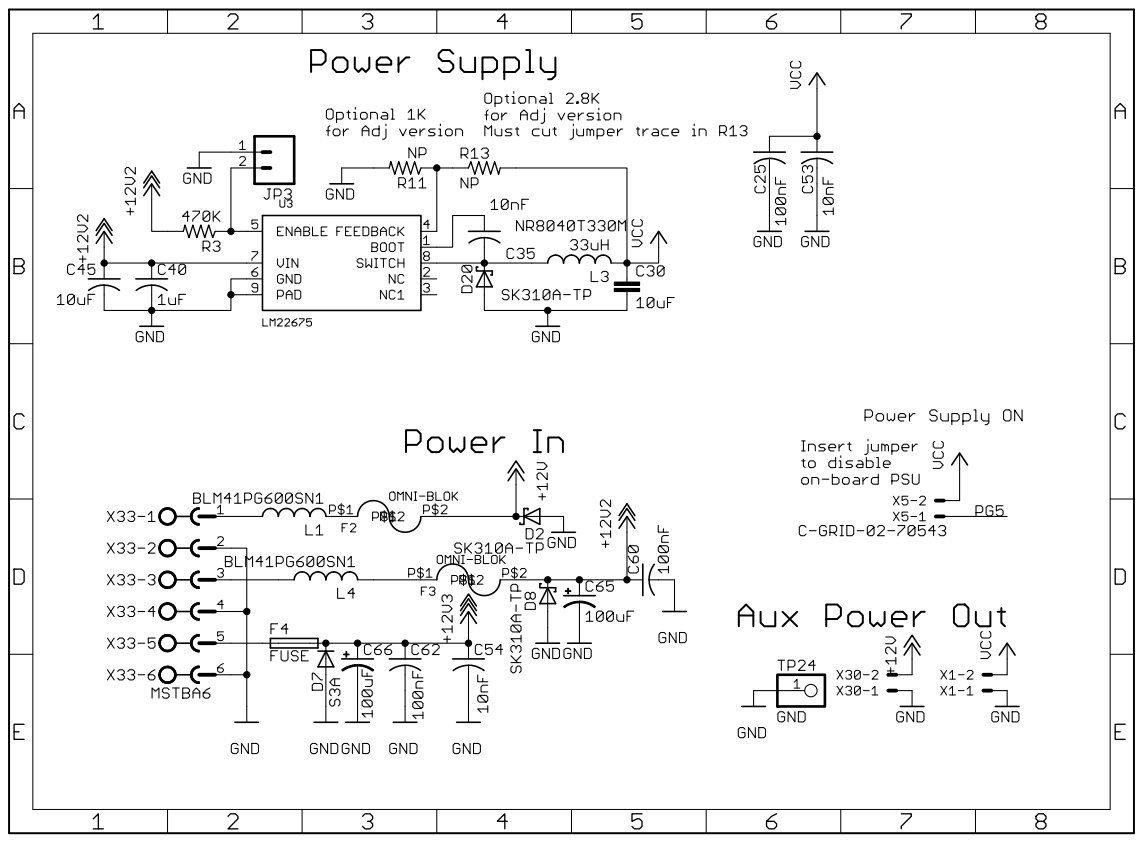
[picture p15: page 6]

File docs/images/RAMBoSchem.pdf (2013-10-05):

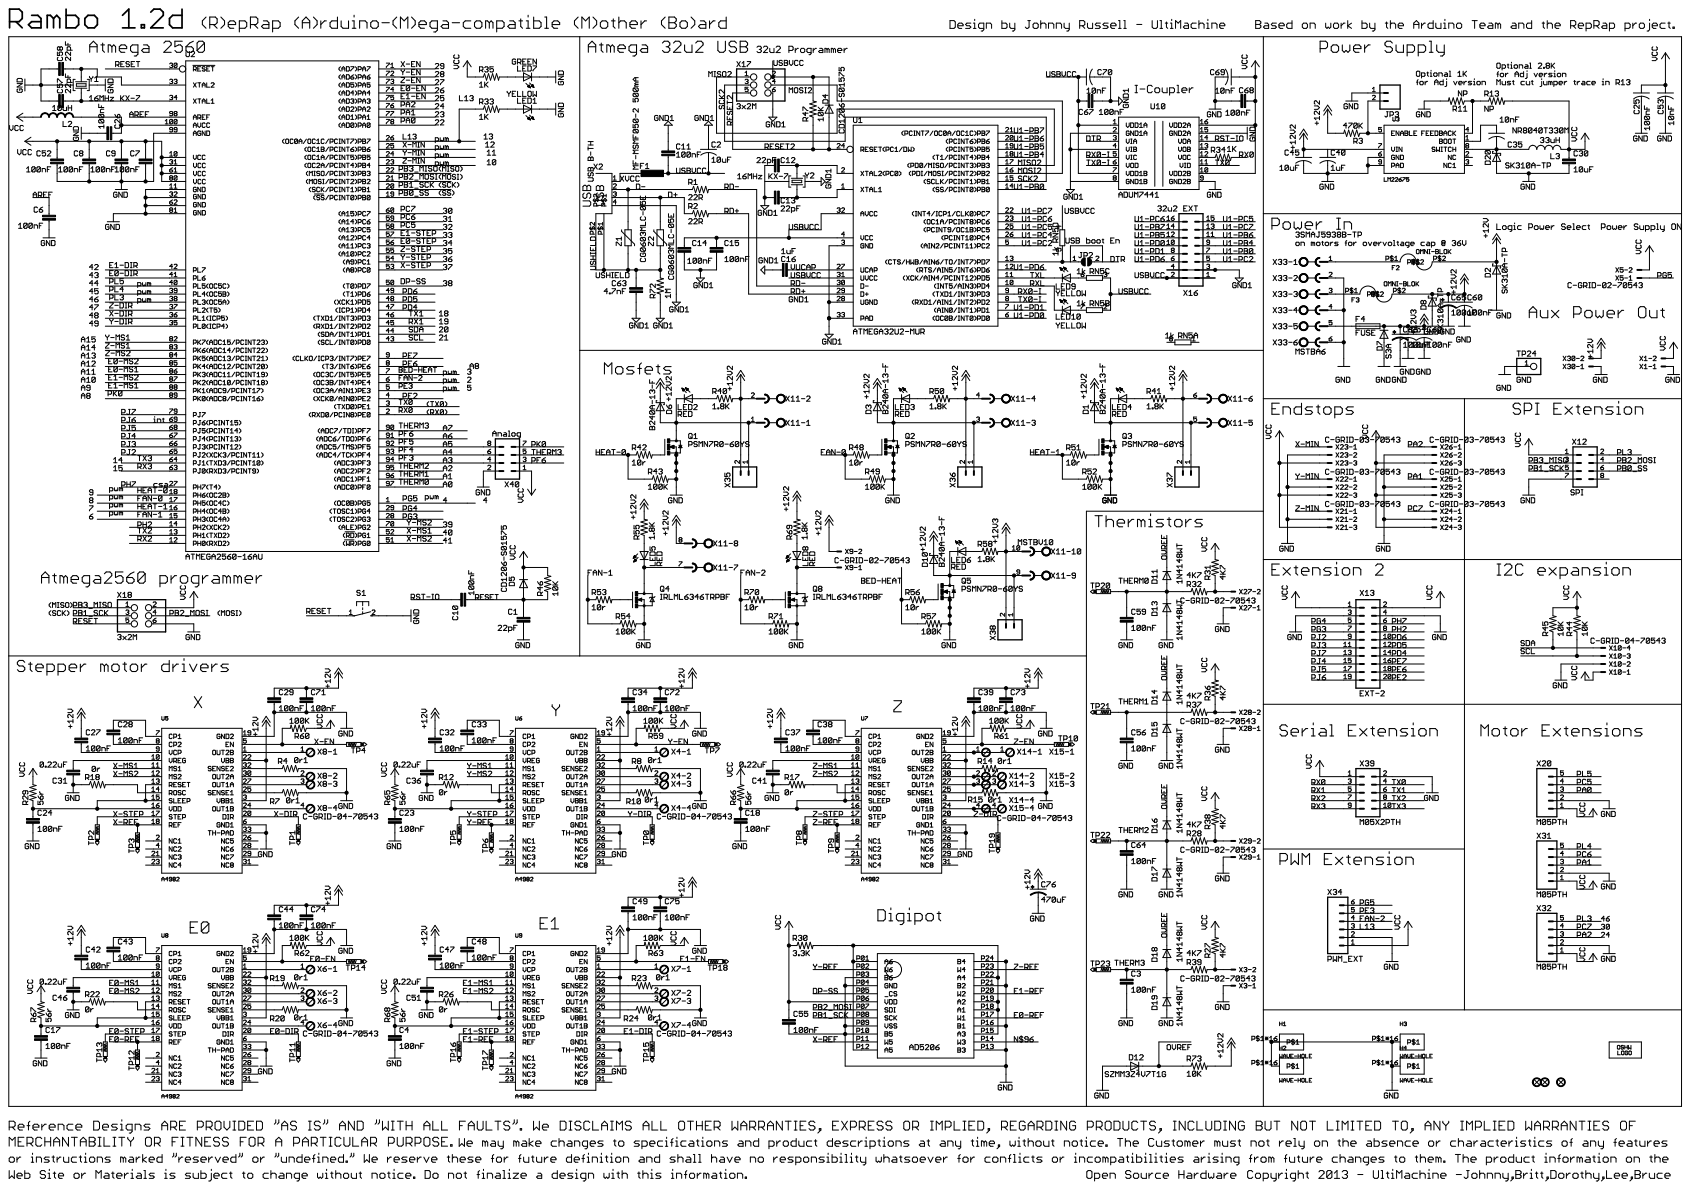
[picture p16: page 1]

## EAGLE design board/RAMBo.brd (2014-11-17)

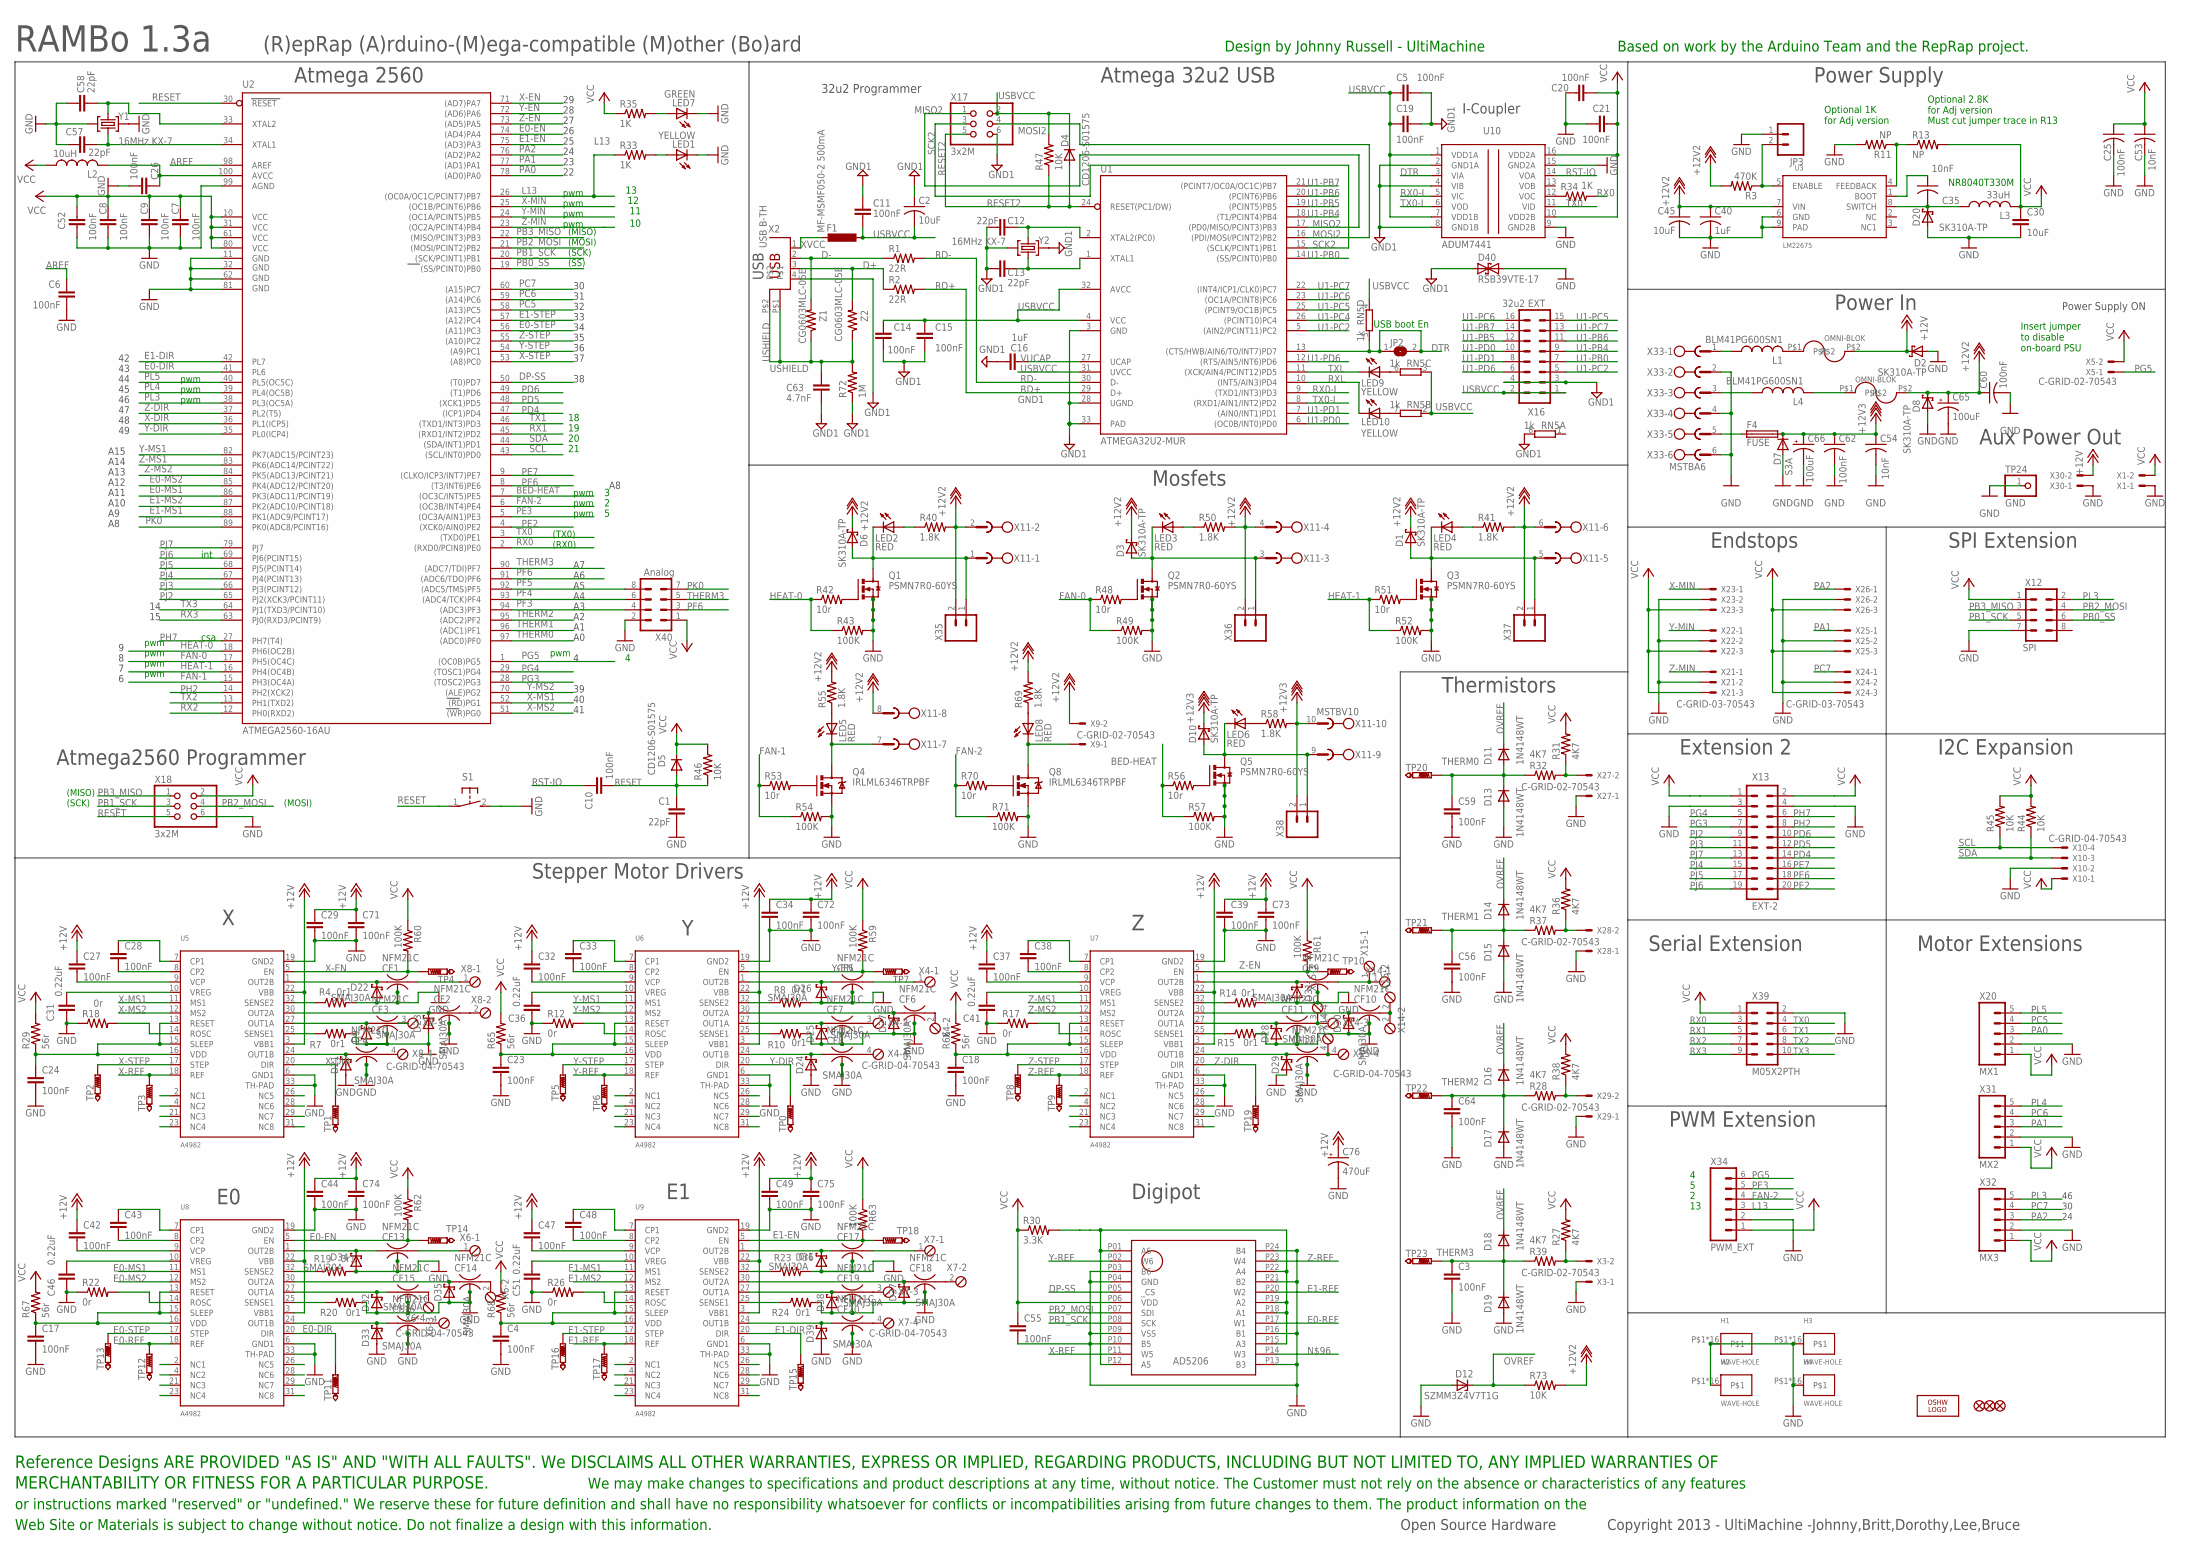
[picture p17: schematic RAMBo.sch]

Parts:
C1, C12, C13, C57, C58: 22pF; C0603
C2: 10uF; C0805
C3, C4, C6, C7, C8, C9, C10, C11, C14, C15, C17, C18, C23, C24, C25, C26, C27, C28, C29, C32, C33, C34, C37, C38, C39, C42, C43, C44, C47, C48, C49, C52, C55, C56, C59, C60, C62, C64, C71, C72, C73, C74, C75: 100nF; C0603
C5, C19, C20, C21: 100nF; C0402
C16: 1uF; C0603
C30: 10uF; C1210K
C31, C36, C41, C46, C51: 0.22uF; C0603
C35, C53, C54: 10nF; C0603
C40: 1uF; C0805
C45: 10uF; C2220K
C63: 4.7nF; C0402
C65, C66: 100uF; E3,5-8
C76: 470uF; C12,5-5
CF1, CF2, CF3, CF4, CF5, CF6, CF7, CF8, CF9, CF10, CF11, CF12, CF13, CF14, CF15, CF16, CF17, CF18, CF19, CF20: NFM21C
D1, D2, D3, D6, D8, D10, D20: SK310A-TP; SMA-SM
D4, D5: CD1206-S01575; MINIMELF
D7: S3A; DO-214AB
D9, D21, D22, D23, D24, D25, D26, D27, D28, D29, D30, D31, D32, D33, D34, D35, D36, D37, D38, D39: SMAJ30A; SMA-SM
D11, D13, D14, D15, D16, D17, D18, D19: 1N4148WT; SOD523
D12: SZMM3Z4V7T1G; SOD323-R
D40: RSB39VTE-17; SOD323-R
F1: MF-MSMF050-2 500mA; L1812
F2, F3: OMNI-BLOK
F4: FUSE; FUSE-ATO-SMD
FID1, FID2, FID3: FIDUCIAL1X2.5; FIDUCIAL-1X2.5
H1, H2, H3, H4: WAVE-HOLE; 3,0-WAVE-HOLE
JP2: SJ
JP3: M02PTH; 1X02
L1, L4: BLM41PG600SN1; L1806
L2: 10uH; C0805
L3: 33uH; NR8040
LED1, LED9, LED10: YELLOW; CHIP-LED0805
LED2, LED3, LED4, LED5, LED6, LED8: RED; CHIP-LED0805
LED7: GREEN; CHIP-LED0805
LOGO1: OSHW_LOGO_8MILX0150-NT; OSHW_8X150_NOTEXT
Q1, Q2, Q3, Q5: PSMN7R0-60YS; SOT669
Q4, Q8: IRLML6346TRPBF; SOT23-3
R1, R2: 22R; R0402
R3: 470K; R0603
R4, R7, R8, R10, R14, R15, R19, R20, R23, R24: 0r1; R1206
R11, R13: NP; R0603
R12, R17, R18, R22, R26: 0r; R0603
R27, R28, R31, R32, R36, R37, R38, R39: 4K7; R0603
R29, R65, R66, R67, R68: 56r; R0603
R30: 3.3K; R0603
R33, R34, R35: 1K; R0603
R40, R41, R50, R55, R58, R69: 1.8K; R0603
R42, R48, R51, R53, R56, R70: 10r; R0603
R43, R49, R52, R54, R57, R59, R60, R61, R62, R63, R71: 100K; R0603
R44, R45, R46, R47, R73: 10K; R0603
R72: 1M; R0402
RN5: 1k; CAY16
S1: 31-XX; B3F-31XX
TP0, TP1, TP2, TP3, TP4, TP5, TP6, TP7, TP8, TP9, TP10, TP11, TP12, TP13, TP14, TP15, TP16, TP17, TP18, TP19: PTR1B1,27TH; B1,27TH
TP20, TP21, TP22, TP23: PTR1B1,27; B1,27
TP24: GND; 1X01
U1: ATMEGA32U2-MUR; QFN32TROUND
U2: ATMEGA2560-16AU; TQFP100
U3: LM22675; SOIC127P600X170-9N
U4: AD5206; TSSOP24
U5, U6, U7, U8, U9: A4982; QFN32TROUND
U10: ADUM7441; QSOP16
X1, X3, X5, X9, X27, X28, X29, X30: C-GRID-02-70543; 70543-02
X2: USB B-TH; PN61729
X4, X6, X7, X8, X14, X15: C-GRID-04-70543; 4POL254
X10: C-GRID-04-70543; 70543-04
X11: MSTBV10
X12: SPI; 2X4
X13: EXT-2; 2X10
X16: 32u2 EXT; 2X8
X17, X18: 3x2M; 2X03
X20: MX1; 1X05
X21, X22, X23, X24, X25, X26: C-GRID-03-70543; 70543-03
X31: MX2; 1X05
X32: MX3; 1X05
X33: MSTBA6
X34: PWM_EXT; 1X06
X35, X36, X37, X38: M02PTH; 1X02
X39: M05X2PTH; AVR_ICSP
X40: Analog; 2X4
Y1, Y2: 16MHz KX-7; CRYSTAL-3.2-2.5
Z1, Z2: CG0603MLC-05E; R0603

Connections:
+12V: C27.1, C29.1, C32.1, C34.1, C37.1, C39.1, C42.1, C44.1, C47.1, C49.1, C71.1, C72.1, C73.1, C74.1, C75.1, C76.+, D2.C, F2.P$2, U5.3 (VBB1), U5.22 (VBB), U6.3 (VBB1), U6.22 (VBB), U7.3 (VBB1), U7.22 (VBB), U8.3 (VBB1), U8.22 (VBB), U9.3 (VBB1), U9.22 (VBB), X30.2
+12V2: C40.1, C45.1, C60.1, C65.+, D1.C, D3.C, D6.C, D8.C, F3.P$2, R3.2, R40.2, R41.2, R50.2, R55.2, R69.2, R73.2, U3.7 (VIN), X9.2, X11.2, X11.4, X11.6, X11.8, X35.2, X36.2, X37.2
+12V3: C54.1, C62.1, C66.+, D7.C, D10.C, F4.P$2 (2), R58.2, X11.10, X38.2
AREF: C6.1, U2.98 (AREF)
BED-HEAT: R56.1, R57.1, U2.7 ((OC3C/INT5)PE5)
D+: R2.1, X2.3, Z2.2
D-: R1.1, X2.2, Z1.2
DP-SS: U2.50 ((T0)PD7), U4.P05 (_CS)
DTR: JP2.1, JP2.2, RN5.5 (2), U1.13 ((CTS/HWB/AIN6/TO/INT7)PD7), U10.3 (VIA)
E0-DIR: TP11.TP, U2.41 (PL6), U8.20 (DIR)
E0-EN: R62.2, TP14.TP, U2.74 ((AD4)PA4), U8.5 (EN)
E0-MS1: U2.86 (PK3(ADC11/PCINT19)), U8.11 (MS1)
E0-MS2: U2.85 (PK4(ADC12/PCINT20)), U8.12 (MS2)
E0-REF: TP12.TP, U4.P17 (W1), U8.18 (REF)
E0-STEP: TP13.TP, U2.56 ((A11)PC3), U8.17 (STEP)
E1-DIR: TP15.TP, U2.42 (PL7), U9.20 (DIR)
E1-EN: R63.2, TP18.TP, U2.75 ((AD3)PA3), U9.5 (EN)
E1-MS1: U2.88 (PK1(ADC9/PCINT17)), U9.11 (MS1)
E1-MS2: U2.87 (PK2(ADC10/PCINT18)), U9.12 (MS2)
E1-REF: TP17.TP, U4.P20 (W2), U9.18 (REF)
E1-STEP: TP16.TP, U2.57 ((A12)PC4), U9.17 (STEP)
FAN-0: R48.1, R49.1, U2.17 (PH5(OC4C))
FAN-1: R53.1, R54.1, U2.15 (PH3(OC4A))
FAN-2: R70.1, R71.1, U2.6 ((OC3B/INT4)PE4), X34.4
GND: C1.2, C3.2, C4.2, C6.2, C7.2, C8.2, C9.2, C17.2, C18.2, C20.2, C21.1, C23.2, C24.2, C25.2, C26.2, C29.2, C30.2, C31.1, C34.2, C36.1, C39.2, C40.2, C41.1, C44.2, C45.2, C46.1, C49.2, C51.1, C52.2, C53.2, C54.2, C55.2, C56.2, C57.2, C58.2, C59.2, C60.2, C62.2, C64.2, C65.-, C66.-, C71.2, C72.2, C73.2, C74.2, C75.2, C76.-, CF1.2@1 (2), CF1.2@2 (2), CF2.2@1 (2), CF2.2@2 (2), CF3.2@1 (2), CF3.2@2 (2), CF4.2@1 (2), CF4.2@2 (2), CF5.2@1 (2), CF5.2@2 (2), CF6.2@1 (2), CF6.2@2 (2), CF7.2@1 (2), CF7.2@2 (2), CF8.2@1 (2), CF8.2@2 (2), CF9.2@1 (2), CF9.2@2 (2), CF10.2@1 (2), CF10.2@2 (2), CF11.2@1 (2), CF11.2@2 (2), CF12.2@1 (2), CF12.2@2 (2), CF13.2@1 (2), CF13.2@2 (2), CF14.2@1 (2), CF14.2@2 (2), CF15.2@1 (2), CF15.2@2 (2), CF16.2@1 (2), CF16.2@2 (2), CF17.2@1 (2), CF17.2@2 (2), CF18.2@1 (2), CF18.2@2 (2), CF19.2@1 (2), CF19.2@2 (2), CF20.2@1 (2), CF20.2@2 (2), D2.A, D7.A, D8.A, D9.A, D12.A, D13.A, D15.A, D17.A, D19.A, D20.A, D21.A, D22.A, D23.A, D24.A, D25.A, D26.A, D27.A, D28.A, D29.A, D30.A, D31.A, D32.A, D33.A, D34.A, D35.A, D36.A, D37.A, D38.A, D39.A, D40.C (2), H1.P$1, H1.P$2, H1.P$3, H1.P$4, H1.P$5, H1.P$6, H1.P$7, H1.P$8, H1.P$17, H1.P$18, H1.P$19, H1.P$20, H1.P$21, H1.P$22, H1.P$23, H1.P$24, H2.P$1, H2.P$2, H2.P$3, H2.P$4, H2.P$5, H2.P$6, H2.P$7, H2.P$8, H2.P$17, H2.P$18, H2.P$19, H2.P$20, H2.P$21, H2.P$22, H2.P$23, H2.P$24, H3.P$1, H3.P$2, H3.P$3, H3.P$4, H3.P$5, H3.P$6, H3.P$7, H3.P$8, H3.P$17, H3.P$18, H3.P$19, H3.P$20, H3.P$21, H3.P$22, H3.P$23, H3.P$24, H4.P$1, H4.P$2, H4.P$3, H4.P$4, H4.P$5, H4.P$6, H4.P$7, H4.P$8, H4.P$17, H4.P$18, H4.P$19, H4.P$20, H4.P$21, H4.P$22, H4.P$23, H4.P$24, JP3.1, LED1.C, LED7.C, Q1.1 (S), Q1.2 (S), Q1.3 (S), Q2.1 (S), Q2.2 (S), Q2.3 (S), Q3.1 (S), Q3.2 (S), Q3.3 (S), Q4.2 (S), Q5.1 (S), Q5.2 (S), Q5.3 (S), Q8.2 (S), R4.2, R7.2, R8.2, R10.2, R11.2, R12.1, R14.2, R15.2, R17.1, R18.1, R19.2, R20.2, R22.1, R23.2, R24.2, R26.1, R43.2, R49.2, R52.2, R54.2, R57.2, R71.2, S1.2 (S), TP24.1, U2.11 (GND), U2.32 (GND1), U2.62 (GND2), U2.81 (GND3), U2.99 (AGND), U3.6 (GND), U3.9 (PAD), U4.P03 (B6), U4.P04 (GND), U4.P09 (VSS), U4.P10 (B5), U4.P13 (B3), U4.P16 (B1), U4.P21 (B2), U4.P24 (B4), U5.6 (GND1), U5.19 (GND2), U5.33 (TH-PAD), U6.6 (GND1), U6.19 (GND2), U6.33 (TH-PAD), U7.6 (GND1), U7.19 (GND2), U7.33 (TH-PAD), U8.6 (GND1), U8.19 (GND2), U8.33 (TH-PAD), U9.6 (GND1), U9.19 (GND2), U9.33 (TH-PAD), U10.9 (GND2B), U10.15 (GND2A), X1.1, X3.1, X10.2, X12.7, X13.3, X13.4, X18.6, X20.2, X21.2, X22.2, X23.2, X24.2, X25.2, X26.2, X27.1, X28.1, X29.1, X30.1, X31.2, X32.2, X33.2, X33.4, X33.6, X34.2, X39.2, X40.2, Y1.2 (GND), Y1.4 (GND)
GND1: C2.1, C5.2, C11.2, C12.2, C13.2, C14.2, C15.2, C16.2, C19.2, C63.2, D40.A (1), R72.1, RN5.8 (2), U1.3 (GND), U1.28 (UGND), U1.33 (PAD), U10.2 (GND1A), U10.4 (VIB), U10.8 (GND1B), X2.4, X16.3, X16.4, X17.6, Y2.2 (GND), Y2.4 (GND)
HEAT-0: R42.1, R43.1, U2.18 (PH6(OC2B))
HEAT-1: R51.1, R52.1, U2.16 (PH4(OC4B))
L13: R33.1, U2.26 ((OC0A/OC1C/PCINT7)PB7), X34.3
MISO2: U1.17 ((PD0/MISO/PCINT3)PB3), X17.1
MOSI2: U1.16 ((PDI/MOSI/PCINT2)PB2), X17.4
unnamed: C31.2, U5.10 (VREG)
unnamed: LED1.A, R33.2
unnamed: LED7.A, R35.2
unnamed: R8.1, U6.32 (SENSE2)
unnamed: R10.1, U6.25 (SENSE1)
unnamed: C33.2, U6.8 (CP2)
unnamed: C32.2, U6.9 (VCP)
unnamed: C36.2, U6.10 (VREG)
unnamed: R12.2, U6.14 (ROSC)
unnamed: Q4.1 (G), R53.2
unnamed: LED10.A, RN5.7 (2)
unnamed: C24.1, R29.1, U5.13 (RESET), U5.15 (SLEEP), U5.16 (VDD)
unnamed: L1.P$1 (1), X33.1
unnamed: F3.P$1, L4.P$2 (2)
unnamed: JP3.2, R3.1, U3.5 (ENABLE)
unnamed: F4.P$1 (1), X33.5
unnamed: CF5.1, D26.C, U6.1 (OUT2B)
unnamed: CF20.3, X7.4
unnamed: CF5.3, X4.1
unnamed: CF6.1, D27.C, U6.30 (OUT2A)
unnamed: D6.A, LED2.C, Q1.MB (D), X11.1, X35.1
unnamed: R4.1, U5.32 (SENSE2)
unnamed: CF7.1, D25.C, U6.27 (OUT1A)
unnamed: C33.1, U6.7 (CP1)
unnamed: C23.1, R65.1, U6.13 (RESET), U6.15 (SLEEP), U6.16 (VDD)
unnamed: Q2.4 (G), R48.2
unnamed: C26.1, L2.2, U2.100 (AVCC)
unnamed: R14.1, U7.32 (SENSE2)
unnamed: R15.1, U7.25 (SENSE1)
unnamed: C38.2, U7.8 (CP2)
unnamed: C37.2, U7.9 (VCP)
unnamed: C41.2, U7.10 (VREG)
unnamed: R17.2, U7.14 (ROSC)
unnamed: CF10.1, D30.C, U7.30 (OUT2A)
unnamed: CF11.1, D28.C, U7.27 (OUT1A)
unnamed: R7.1, U5.25 (SENSE1)
unnamed: C28.2, U5.8 (CP2)
unnamed: C27.2, U5.9 (VCP)
unnamed: CF19.3, X7.3
unnamed: CF12.1, D29.C, U7.24 (OUT1B)
unnamed: CF12.3, X14.4, X15.4
unnamed: C38.1, U7.7 (CP1)
unnamed: R18.2, U5.14 (ROSC)
unnamed: C18.1, R66.1, U7.13 (RESET), U7.15 (SLEEP), U7.16 (VDD)
unnamed: LED8.C, Q8.3 (D), X9.1
unnamed: R19.1, U8.32 (SENSE2)
unnamed: CF1.1, D22.C, U5.1 (OUT2B)
unnamed: C28.1, U5.7 (CP1)
unnamed: R20.1, U8.25 (SENSE1)
unnamed: C43.2, U8.8 (CP2)
unnamed: CF3.1, D9.C, U5.27 (OUT1A)
unnamed: CF4.1, D21.C, U5.24 (OUT1B)
unnamed: LED9.A, RN5.6 (2)
unnamed: R34.1, U10.12 (VOC)
unnamed: C42.2, U8.9 (VCP)
unnamed: C46.2, U8.10 (VREG)
unnamed: R22.2, U8.14 (ROSC)
unnamed: CF13.1, D34.C, U8.1 (OUT2B)
unnamed: CF13.3, X6.1
unnamed: CF14.1, D35.C, U8.30 (OUT2A)
unnamed: CF15.1, D32.C, U8.27 (OUT1A)
unnamed: C43.1, U8.7 (CP1)
unnamed: C17.1, R67.1, U8.13 (RESET), U8.15 (SLEEP), U8.16 (VDD)
unnamed: CF18.3, X7.2
unnamed: R23.1, U9.32 (SENSE2)
unnamed: R24.1, U9.25 (SENSE1)
unnamed: C48.2, U9.8 (CP2)
unnamed: C47.2, U9.9 (VCP)
unnamed: C51.2, U9.10 (VREG)
unnamed: R26.2, U9.14 (ROSC)
unnamed: CF20.1, D39.C, U9.24 (OUT1B)
unnamed: CF19.1, D38.C, U9.27 (OUT1A)
unnamed: CF17.1, D36.C, U9.1 (OUT2B)
unnamed: CF18.1, D37.C, U9.30 (OUT2A)
unnamed: C48.1, U9.7 (CP1)
unnamed: C4.1, R68.1, U9.13 (RESET), U9.15 (SLEEP), U9.16 (VDD)
unnamed: LED8.A, R69.1
unnamed: Q8.1 (G), R70.2
unnamed: LED2.A, R40.1
unnamed: R30.2, U4.P01 (A6), U4.P12 (A5), U4.P15 (A3), U4.P18 (A1), U4.P19 (A2), U4.P22 (A4)
unnamed: R31.1, R32.2, X27.2
unnamed: Q1.4 (G), R42.2
unnamed: R36.1, R37.2, X28.2
unnamed: Q3.4 (G), R51.2
unnamed: R28.2, R38.1, X29.2
unnamed: Q5.4 (G), R56.2
unnamed: CF17.3, X7.1
unnamed: CF16.3, X6.4
unnamed: CF15.3, X6.3
unnamed: D3.A, LED3.C, Q2.MB (D), X11.3, X36.1
unnamed: LED3.A, R50.1
unnamed: D1.A, LED4.C, Q3.MB (D), X11.5, X37.1
unnamed: LED4.A, R41.1
unnamed: LED5.C, Q4.3 (D), X11.7
unnamed: LED5.A, R55.1
unnamed: D10.A, LED6.C, Q5.MB (D), X11.9, X38.1
unnamed: LED6.A, R58.1
unnamed: CF14.3, X6.2
unnamed: CF16.1, D33.C, U8.24 (OUT1B)
unnamed: CF4.3, X8.4
unnamed: CF3.3, X8.3
unnamed: R27.1, R39.2, X3.2
unnamed: CF2.3, X8.2
unnamed: C35.1, U3.1 (BOOT)
unnamed: CF1.3, X8.1
unnamed: CF8.3, X4.4
unnamed: CF7.3, X4.3
unnamed: R11.1, R13.1, U3.4 (FEEDBACK)
unnamed: C35.2, D20.C, L3.P$1 (1), U3.8 (SWITCH)
unnamed: CF6.3, X4.2
unnamed: CF8.1, D24.C, U6.24 (OUT1B)
unnamed: CF9.1, D31.C, U7.1 (OUT2B)
unnamed: CF11.3, X14.3, X15.3
unnamed: CF9.3, X14.1, X15.1
unnamed: CF10.3, X14.2, X15.2
unnamed: F2.P$1, L1.P$2 (2)
unnamed: CF2.1, D23.C, U5.30 (OUT2A)
unnamed: L4.P$1 (1), X33.3
OVREF: D11.C, D12.C, D14.C, D16.C, D18.C, R73.1
PA0: U2.78 ((AD0)PA0), X20.3
PA1: U2.77 ((AD1)PA1), X25.1, X31.3
PA2: U2.76 ((AD2)PA2), X26.1, X32.3
PB0_SS: U2.19 ((SS/PCINT0)PB0), X12.6
PB1_SCK: U2.20 ((SCK/PCINT1)PB1), U4.P08 (SCK), X12.5, X18.3
PB2_MOSI: U2.21 ((MOSI/PCINT2)PB2), U4.P07 (SDI), X12.4, X18.4
PB3_MISO: U2.22 ((MISO/PCINT3)PB3), X12.3, X18.1
PC5: U2.58 ((A13)PC5), X20.4
PC6: U2.59 ((A14)PC6), X31.4
PC7: U2.60 ((A15)PC7), X24.1, X32.4
PD4: U2.47 ((ICP1)PD4), X13.14
PD5: U2.48 ((XCK1)PD5), X13.12
PD6: U2.49 ((T1)PD6), X13.10
PE2: U2.4 ((XCK0/AIN0)PE2), X13.20
PE3: U2.5 ((OC3A/AIN1)PE3), X34.5
PE6: U2.8 ((T3/INT6)PE6), X13.18
PE7: U2.9 ((CLKO/ICP3/INT7)PE7), X13.16
PF3: U2.94 ((ADC3)PF3), X40.4
PF4: U2.93 ((ADC4/TCK)PF4), X40.6
PF5: U2.92 ((ADC5/TMS)PF5), X40.8
PF6: U2.91 ((ADC6/TDO)PF6), X40.3
PG3: U2.28 ((TOSC2)PG3), X13.7
PG4: U2.29 ((TOSC1)PG4), X13.5
PG5: U2.1 ((OC0B)PG5), X5.1, X34.6
PH2: U2.14 (PH2(XCK2)), X13.8
PH7: U2.27 (PH7(T4)), X13.6
PJ2: U2.65 (PJ2(XCK3/PCINT11)), X13.9
PJ3: U2.66 (PJ3(PCINT12)), X13.11
PJ4: U2.67 (PJ4(PCINT13)), X13.15
PJ5: U2.68 (PJ5(PCINT14)), X13.17
PJ6: U2.69 (PJ6(PCINT15)), X13.19
PJ7: U2.79 (PJ7), X13.13
PK0: U2.89 (PK0(ADC8/PCINT16)), X40.7
PL3: U2.38 (PL3(OC5A)), X12.2, X32.5
PL4: U2.39 (PL4(OC5B)), X31.5
PL5: U2.40 (PL5(OC5C)), X20.5
RD+: R2.2, U1.29 (D+)
RD-: R1.2, U1.30 (D-)
RESET: C1.1, C10.2, D5.A, R46.1, S1.1, U2.30 (RESET), X18.5
RESET2: D4.A, R47.1, U1.24 (RESET(PC1/DW)), X17.5
RST-IO: C10.1, U10.14 (VOA)
RX0: R34.2, U2.2 ((RXD0/PCIN8)PE0), X39.3
RX0-I: U1.9 ((TXD1/INT3)PD3), U10.5 (VIC)
RX1: U2.45 ((RXD1/INT2)PD2), X39.5
RX2: U2.12 (PH0(RXD2)), X39.7
RX3: U2.63 (PJ0(RXD3/PCINT9)), X39.9
RXL: LED10.C, U1.10 ((INT5/AIN3)PD4)
SCK2: U1.15 ((SCLK/PCINT1)PB1), X17.3
SCL: R45.1, U2.43 ((SCL/INT0)PD0), X10.4
SDA: R44.1, U2.44 ((SDA/INT1)PD1), X10.3
THERM0: C59.1, D11.A, D13.C, R32.1, TP20.TP, U2.97 ((ADC0)PF0)
THERM1: C56.1, D14.A, D15.C, R37.1, TP21.TP, U2.96 ((ADC1)PF1)
THERM2: C64.1, D16.A, D17.C, R28.1, TP22.TP, U2.95 ((ADC2)PF2)
THERM3: C3.1, D18.A, D19.C, R39.1, TP23.TP, U2.90 ((ADC7/TDI)PF7), X40.5
TX0: U2.3 ((TXD0)PE1), U10.11 (VID), X39.4
TX0-I: U1.8 ((RXD1/AIN1/INT2)PD2), U10.6 (VOD)
TX1: U2.46 ((TXD1/INT3)PD3), X39.6
TX2: U2.13 (PH1(TXD2)), X39.8
TX3: U2.64 (PJ1(TXD3/PCINT10)), X39.10
TXL: LED9.C, U1.11 ((XCK/AIN4/PCINT12)PD5)
U1-PB0: U1.14 ((SS/PCINT0)PB0), X16.7
U1-PB4: U1.18 ((T1/PCINT4)PB4), X16.9
U1-PB5: U1.19 ((PCINT5)PB5), X16.12
U1-PB6: U1.20 ((PCINT6)PB6), X16.11
U1-PB7: U1.21 ((PCINT7/OC0A/OC1C)PB7), X16.14
U1-PC2: U1.5 ((AIN2/PCINT11)PC2), X16.5
U1-PC4: U1.26 ((PCINT10)PC4)
U1-PC5: U1.25 ((PCINT9/OC1B)PC5), X16.15
U1-PC6: U1.23 ((OC1A/PCINT8)PC6), X16.16
U1-PC7: U1.22 ((INT4/ICP1/CLK0)PC7), X16.13
U1-PD0: U1.6 ((OC0B/INT0)PD0), X16.10
U1-PD1: U1.7 ((AIN0/INT1)PD1), X16.8
U1-PD6: U1.12 ((RTS/AIN5/INT6)PD6), X16.6
USBVCC: C2.2, C5.1, C11.1, C14.1, C15.1, C19.1, D4.C, F1.1, R47.2, RN5.2 (1), RN5.3 (1), RN5.4 (1), U1.4 (VCC), U1.31 (UVCC), U1.32 (AVCC), U10.1 (VDD1A), U10.7 (VDD1B), X16.1, X16.2, X17.2
USHIELD: C63.1, R72.2, X2.P$1, X2.P$2, Z1.1, Z2.1
VCC: C7.1, C8.1, C9.1, C20.1, C21.2, C25.1, C30.1, C52.1, C53.1, C55.1, D5.C, L2.1, L3.P$2 (2), R13.2, R27.2, R29.2, R30.1, R31.2, R35.1, R36.2, R38.2, R44.2, R45.2, R46.2, R59.1, R60.1, R61.1, R62.1, R63.1, R65.2, R66.2, R67.2, R68.2, U2.10 (VCC), U2.31 (VCC1), U2.61 (VCC2), U2.80 (VCC3), U4.P06 (VDD), U10.10 (VDD2B), U10.16 (VDD2A), X1.2, X5.2, X10.1, X12.1, X13.1, X13.2, X18.2, X20.1, X21.3, X22.3, X23.3, X24.3, X25.3, X26.3, X31.1, X32.1, X34.1, X39.1, X40.1
VUCAP: C16.1, U1.27 (UCAP)
X-DIR: TP1.TP, U2.36 (PL1(ICP5)), U5.20 (DIR)
X-EN: R60.2, TP4.TP, U2.71 ((AD7)PA7), U5.5 (EN)
X-MIN: U2.25 ((OC1B/PCINT6)PB6), X23.1
X-MS1: U2.52 ((RD)PG1), U5.11 (MS1)
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

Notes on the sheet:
(SCK)
(MISO)
(MOSI)
pwm
(TX0)
(RX0)
USB boot En
int
csa
(SS)
Reference Designs ARE PROVIDED "AS IS" AND "WITH ALL FAULTS". We DISCLAIMS ALL OTHER WARRANTIES, EXPRESS OR IMPLIED, REGARDING PRODUCTS, INCLUDING BUT NOT LIMITED TO, ANY IMPLIED WARRANTIES OF
MERCHANTABILITY OR FITNESS FOR A PARTICULAR PURPOSE.
or instructions marked "reserved" or "undefined." We reserve these for future definition and shall have no responsibility whatsoever for conflicts or incompatibilities arising from future changes to them. The product information on the
Web Site or Materials is subject to change without notice. Do not finalize a design with this information.
A10
A11
A12
A13
A14
A15
Motor Extensions
SPI Extension
PWM Extension
RAMBo 1.3a
Atmega 32u2 USB
I2C Expansion
Atmega2560 Programmer
Power In
Power Supply
Stepper Motor Drivers
Digipot
Thermistors
Mosfets
Aux Power Out
Design by Johnny Russell - UltiMachine
Based on work by the Arduino Team and the RepRap project.
(R)epRap (A)rduino-(M)ega-compatible (M)other (Bo)ard
Serial Extension
Endstops
Atmega 2560

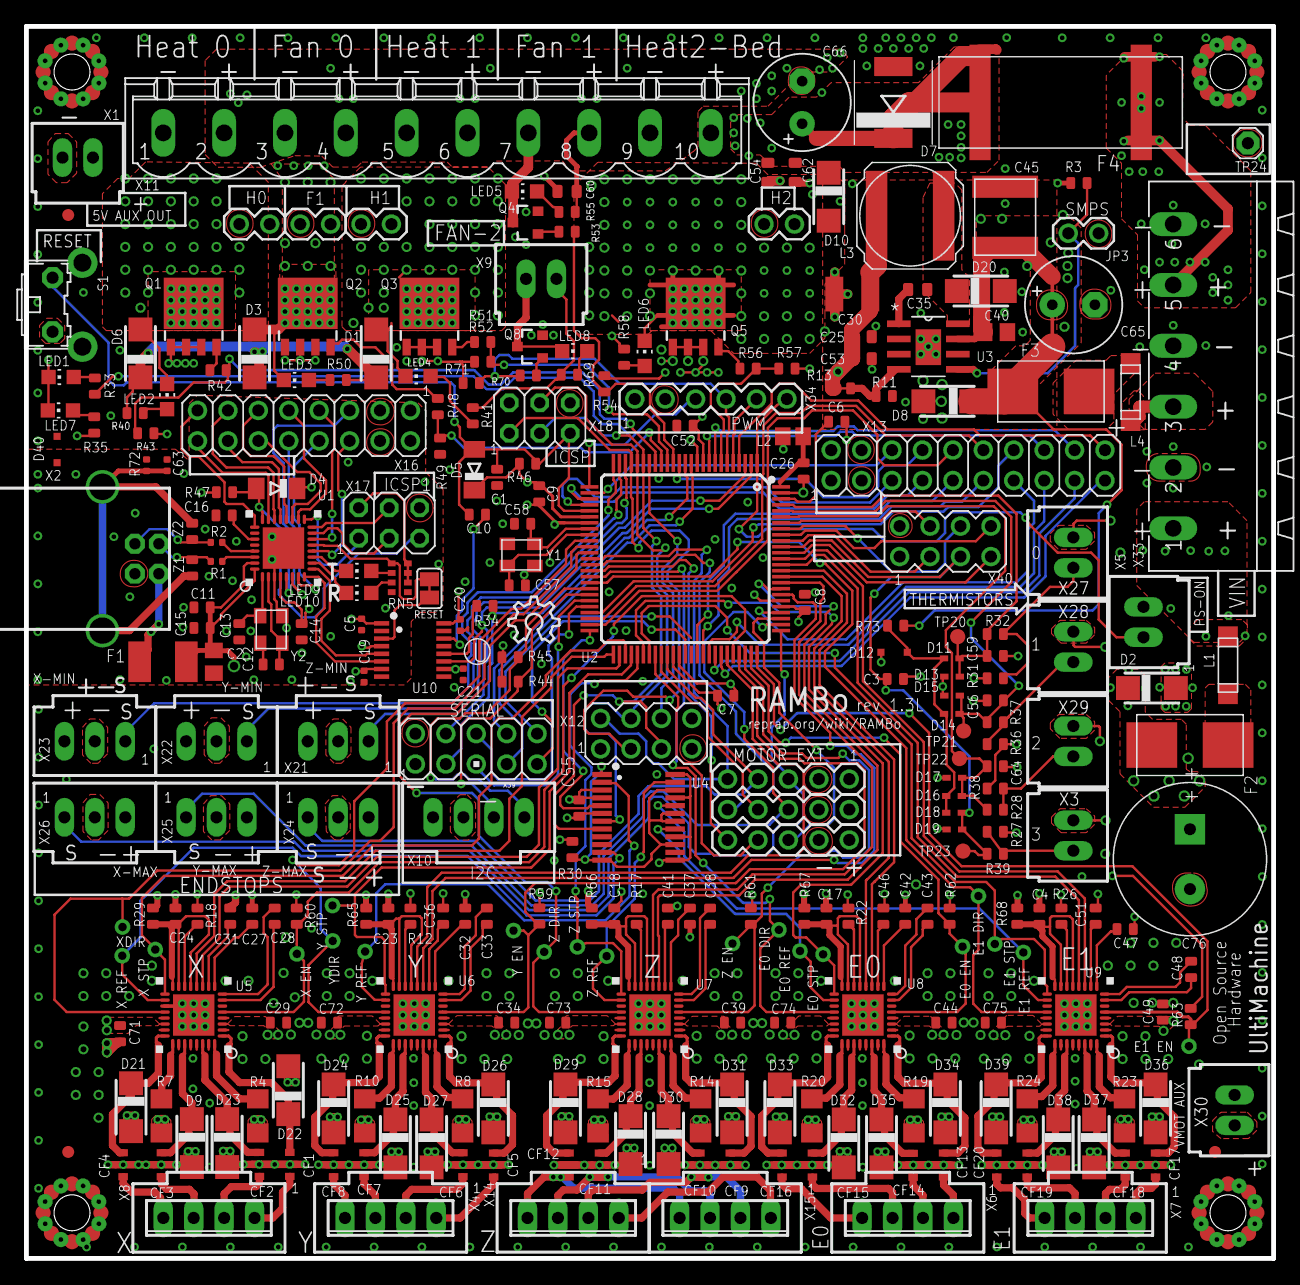
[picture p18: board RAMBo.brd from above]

Board: 4 copper layers, 104.1 x 102.9 mm, 309 parts (0 on the bottom side), 252 nets.

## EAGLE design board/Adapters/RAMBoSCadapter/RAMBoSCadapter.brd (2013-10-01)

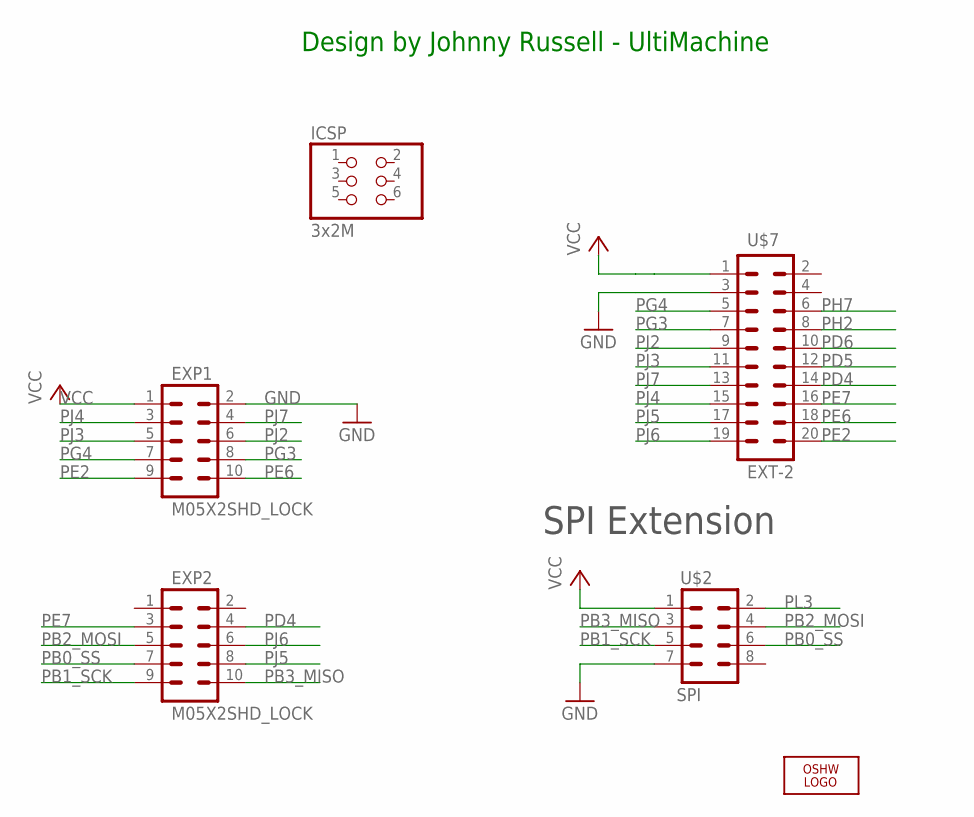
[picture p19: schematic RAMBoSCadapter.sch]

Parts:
EXP1, EXP2: M05X2SHD_LOCK; 2X5-SHROUDED_LOCK
ICSP: 3x2M; 2X03
LOGO1: OSHW_LOGO_8MILX0150-NT; OSHW_8X150_NOTEXT
U$2: SPI; 2X4
U$7: EXT-2; 2X10

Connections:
GND: EXP1.2, U$2.7, U$7.3
PB0_SS: EXP2.7, U$2.6
PB1_SCK: EXP2.9, U$2.5
PB2_MOSI: EXP2.5, U$2.4
PB3_MISO: EXP2.10, U$2.3
PD4: EXP2.4, U$7.14
PD5: U$7.12
PD6: U$7.10
PE2: EXP1.9, U$7.20
PE6: EXP1.10, U$7.18
PE7: EXP2.3, U$7.16
PG3: EXP1.8, U$7.7
PG4: EXP1.7, U$7.5
PH2: U$7.8
PH7: U$7.6
PJ2: EXP1.6, U$7.9
PJ3: EXP1.5, U$7.11
PJ4: EXP1.3, U$7.15
PJ5: EXP2.8, U$7.17
PJ6: EXP2.6, U$7.19
PJ7: EXP1.4, U$7.13
PL3: U$2.2
VCC: EXP1.1, U$2.1, U$7.1

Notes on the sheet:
SPI Extension
Design by Johnny Russell - UltiMachine

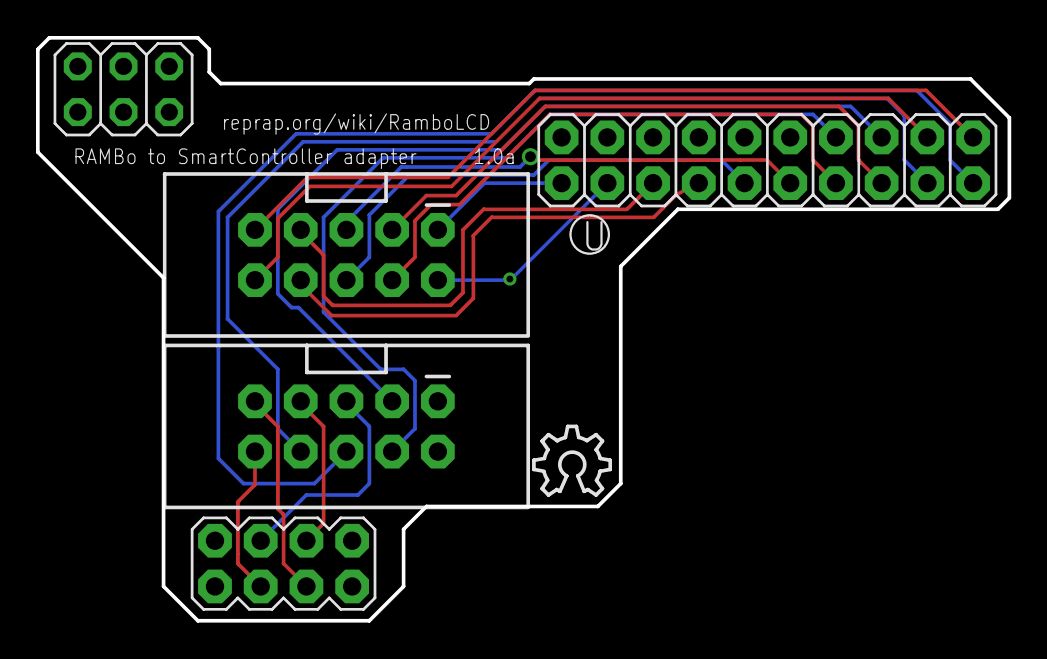
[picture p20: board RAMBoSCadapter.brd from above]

Board: 2 copper layers, 54.0 x 32.4 mm, 6 parts (0 on the bottom side), 18 nets.

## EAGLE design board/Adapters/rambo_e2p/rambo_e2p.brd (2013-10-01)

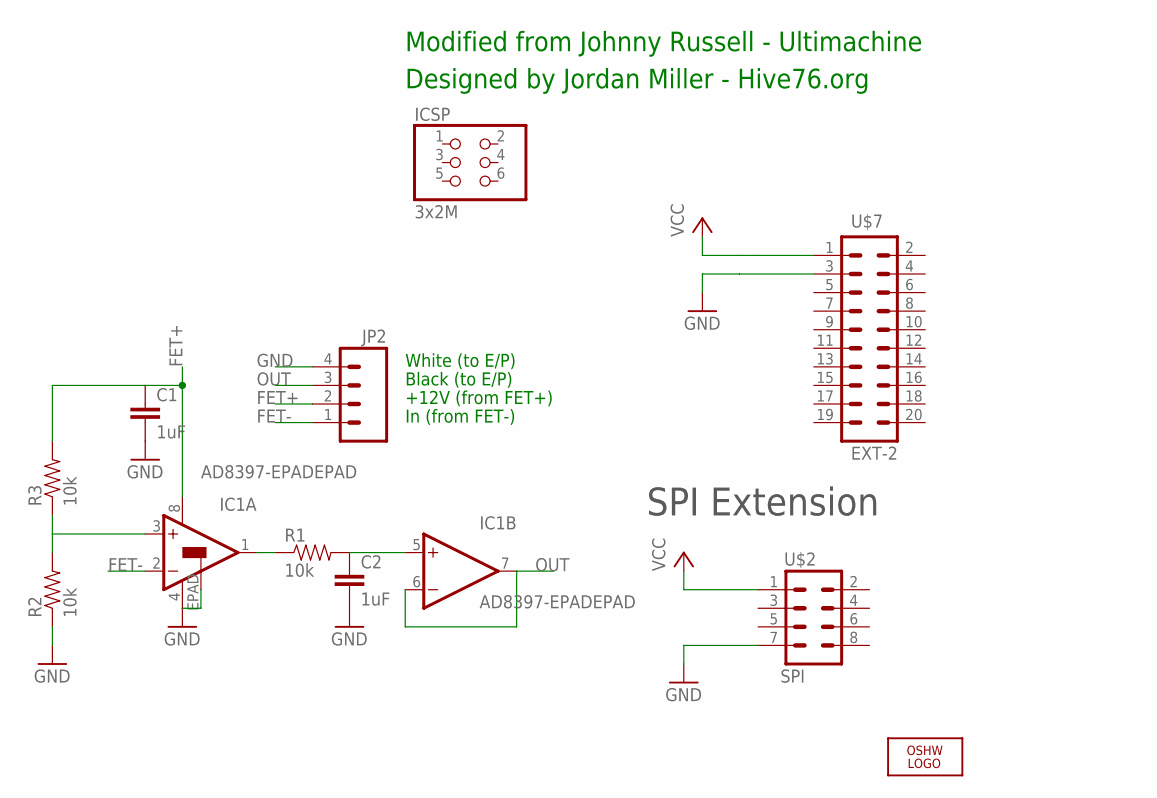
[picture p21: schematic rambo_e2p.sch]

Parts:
C1, C2: 1uF; 0805
IC1: AD8397-EPADEPAD; SO08-EPAD
ICSP: 3x2M; 2X03
JP2: M04SCREW; SCREWTERMINAL-3.5MM-4
LOGO1: OSHW_LOGO_8MILX0150-NT; OSHW_8X150_NOTEXT
R1, R2, R3: 10k; 0805
U$2: SPI; 2X4
U$7: EXT-2; 2X10

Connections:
FET+: C1.1, IC1.8 (V+), JP2.2, R3.2
FET-: IC1.2 (-IN), JP2.1
GND: C1.2, C2.2, IC1.4 (V-), IC1.EPAD, JP2.4, R2.1, U$2.7, U$7.3
unnamed: IC1.1 (OUT), R1.1
unnamed: C2.1, IC1.5 (+IN), R1.2
unnamed: IC1.3 (+IN), R2.2, R3.1
OUT: IC1.6 (-IN), IC1.7 (OUT), JP2.3
VCC: U$2.1, U$7.1

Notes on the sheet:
SPI Extension
+12V (from FET+)
White (to E/P)
Black (to E/P)
In (from FET-)
Modified from Johnny Russell - Ultimachine
Designed by Jordan Miller - Hive76.org

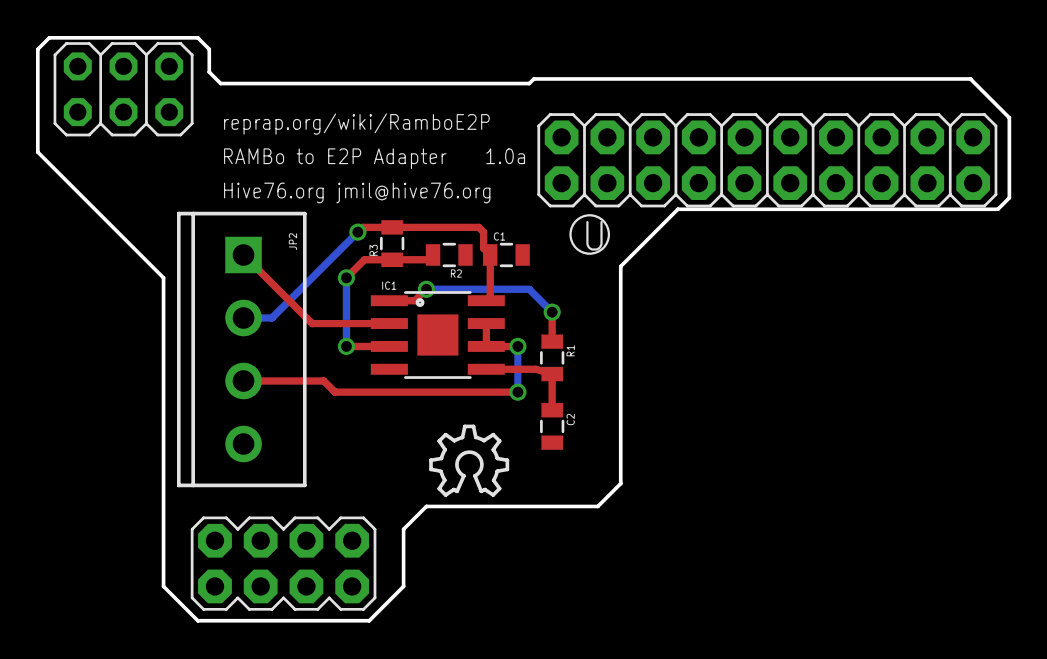
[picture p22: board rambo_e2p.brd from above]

Board: 2 copper layers, 54.0 x 32.4 mm, 11 parts (0 on the bottom side), 8 nets.

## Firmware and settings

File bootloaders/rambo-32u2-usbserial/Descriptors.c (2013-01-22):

/*
             LUFA Library
     Copyright (C) Dean Camera, 2010.
              
  dean [at] fourwalledcubicle [dot] com
      www.fourwalledcubicle.com
*/

/*
  Copyright 2010  Dean Camera (dean [at] fourwalledcubicle [dot] com)

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
  The author disclaim all warranties with regard to this
  software, including all implied warranties of merchantability
  and fitness.  In no event shall the author be liable for any
  special, indirect or consequential damages or any damages
  whatsoever resulting from loss of use, data or profits, whether
  in an action of contract, negligence or other tortious action,
  arising out of or in connection with the use or performance of
  this software.
*/

/** \file
 *
 *  USB Device Descriptors, for library use when in USB device mode. Descriptors are special 
 *  computer-readable structures which the host requests upon device enumeration, to determine
 *  the device's capabilities and functions.  
 */

#include "Descriptors.h"

/* On some devices, there is a factory set internal serial number which can be automatically sent to the host as
 * the device's serial number when the Device Descriptor's .SerialNumStrIndex entry is set to USE_INTERNAL_SERIAL.
 * This allows the host to track a device across insertions on different ports, allowing them to retain allocated
 * resources like COM port numbers and drivers. On demos using this feature, give a warning on unsupported devices
 * so that the user can supply their own serial number descriptor instead or remove the USE_INTERNAL_SERIAL value
 * from the Device Descriptor (forcing the host to generate a serial number for each device from the VID, PID and
 * port location).
 */
#if (USE_INTERNAL_SERIAL == NO_DESCRIPTOR)
	#warning USE_INTERNAL_SERIAL is not available on this AVR - please manually construct a device serial descriptor.
#endif

/** Device descriptor structure. This descriptor, located in FLASH memory, describes the overall
 *  device characteristics, including the supported USB version, control endpoint size and the
 *  number of device configurations. The descriptor is read out by the USB host when the enumeration
 *  process begins.
 */
USB_Descriptor_Device_t PROGMEM DeviceDescriptor =
{
	.Header                 = {.Size = sizeof(USB_Descriptor_Device_t), .Type = DTYPE_Device},
		
	.USBSpecification       = VERSION_BCD(01.10),
	.Class                  = 0x02,
	.SubClass               = 0x00,
	.Protocol               = 0x00,
				
	.Endpoint0Size          = FIXED_CONTROL_ENDPOINT_SIZE,
		
	.VendorID               = 0x27B1, // UltiMachine VendorID

	.ProductID          	= 0x0001, // RAMBo
	.ReleaseNumber          = 0x0001,
		
	.ManufacturerStrIndex   = 0x01,
	.ProductStrIndex        = 0x02,
	.SerialNumStrIndex      = USE_INTERNAL_SERIAL,
		
	.NumberOfConfigurations = FIXED_NUM_CONFIGURATIONS
};

/** Configuration descriptor structure. This descriptor, located in FLASH memory, describes the usage
 *  of the device in one of its supported configurations, including information about any device interfaces
 *  and endpoints. The descriptor is read out by the USB host during the enumeration process when selecting
 *  a configuration so that the host may correctly communicate with the USB device.
 */
USB_Descriptor_Configuration_t PROGMEM ConfigurationDescriptor =
{
	.Config = 
		{
			.Header                 = {.Size = sizeof(USB_Descriptor_Configuration_Header_t), .Type = DTYPE_Configuration},

			.TotalConfigurationSize = sizeof(USB_Descriptor_Configuration_t),
			.TotalInterfaces        = 2,
				
			.ConfigurationNumber    = 1,
			.ConfigurationStrIndex  = NO_DESCRIPTOR,
				
			.ConfigAttributes       = (USB_CONFIG_ATTR_BUSPOWERED | USB_CONFIG_ATTR_SELFPOWERED),
			
			.MaxPowerConsumption    = USB_CONFIG_POWER_MA(100)
		},
		
	.CDC_CCI_Interface = 
		{
			.Header                 = {.Size = sizeof(USB_Descriptor_Interface_t), .Type = DTYPE_Interface},

			.InterfaceNumber        = 0,
			.AlternateSetting       = 0,
			
			.TotalEndpoints         = 1,
				
			.Class                  = 0x02,
			.SubClass               = 0x02,
			.Protocol               = 0x01,
				
			.InterfaceStrIndex      = NO_DESCRIPTOR
		},

	.CDC_Functional_IntHeader = 
		{
			.Header                 = {.Size = sizeof(CDC_FUNCTIONAL_DESCRIPTOR(2)), .Type = 0x24},
			.SubType                = 0x00,
			
			.Data                   = {0x01, 0x10}
		},

	.CDC_Functional_AbstractControlManagement = 
		{
			.Header                 = {.Size = sizeof(CDC_FUNCTIONAL_DESCRIPTOR(1)), .Type = 0x24},
			.SubType                = 0x02,
			
			.Data                   = {0x06}
		},
		
	.CDC_Functional_Union = 
		{
			.Header                 = {.Size = sizeof(CDC_FUNCTIONAL_DESCRIPTOR(2)), .Type = 0x24},
			.SubType                = 0x06,
			
			.Data                   = {0x00, 0x01}
		},

	.CDC_NotificationEndpoint = 
		{
			.Header                 = {.Size = sizeof(USB_Descriptor_Endpoint_t), .Type = DTYPE_Endpoint},
			
			.EndpointAddress        = (ENDPOINT_DESCRIPTOR_DIR_IN | CDC_NOTIFICATION_EPNUM),
			.Attributes             = (EP_TYPE_INTERRUPT | ENDPOINT_ATTR_NO_SYNC | ENDPOINT_USAGE_DATA),
			.EndpointSize           = CDC_NOTIFICATION_EPSIZE,
			.PollingIntervalMS      = 0xFF
		},

	.CDC_DCI_Interface = 
		{
			.Header                 = {.Size = sizeof(USB_Descriptor_Interface_t), .Type = DTYPE_Interface},

			.InterfaceNumber        = 1,
			.AlternateSetting       = 0,
			
			.TotalEndpoints         = 2,
				
			.Class                  = 0x0A,
			.SubClass               = 0x00,
			.Protocol               = 0x00,
				
			.InterfaceStrIndex      = NO_DESCRIPTOR
		},

	.CDC_DataOutEndpoint = 
		{
			.Header                 = {.Size = sizeof(USB_Descriptor_Endpoint_t), .Type = DTYPE_Endpoint},
			
			.EndpointAddress        = (ENDPOINT_DESCRIPTOR_DIR_OUT | CDC_RX_EPNUM),
			.Attributes             = (EP_TYPE_BULK | ENDPOINT_ATTR_NO_SYNC | ENDPOINT_USAGE_DATA),
			.EndpointSize           = CDC_TXRX_EPSIZE,
			.PollingIntervalMS      = 0x01
		},
		
	.CDC_DataInEndpoint = 
		{
			.Header                 = {.Size = sizeof(USB_Descriptor_Endpoint_t), .Type = DTYPE_Endpoint},
			
			.EndpointAddress        = (ENDPOINT_DESCRIPTOR_DIR_IN | CDC_TX_EPNUM),
			.Attributes             = (EP_TYPE_BULK | ENDPOINT_ATTR_NO_SYNC | ENDPOINT_USAGE_DATA),
			.EndpointSize           = CDC_TXRX_EPSIZE,
			.PollingIntervalMS      = 0x01
		}
};

/** Language descriptor structure. This descriptor, located in FLASH memory, is returned when the host requests
 *  the string descriptor with index 0 (the first index). It is actually an array of 16-bit integers, which indicate
 *  via the language ID table available at USB.org what languages the device supports for its string descriptors.
 */
USB_Descriptor_String_t PROGMEM LanguageString =
{
	.Header                 = {.Size = USB_STRING_LEN(1), .Type = DTYPE_String},
		
	.UnicodeString          = {LANGUAGE_ID_ENG}
};
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

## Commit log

2012-09-14 add 1.0d files
    [RAMBo.brd]
2012-09-17 removed stop on vias, added stop under drivers
    [RAMBo.brd]
2012-09-17 change R30 value
    [RAMBo.brd]
2012-09-17 clarify PS-ON silk and schematic
    [RAMBo.brd]
2012-09-17 minor silk screen fixes
    [RAMBo.brd]
2012-09-25 fix component names
    [RAMBo.brd]
2012-10-09 add BOM
    [RAMBoBOM.ods]
2012-10-09 move BOM to board folder
    [RAMBoBOM.ods]
2012-10-18 clean up BOM, change part for 0.22uF caps
    [RAMBoBOM.ods]
2012-12-05 change F1, redo layout mosfets and motor drivers
    [RAMBo.brd]
2012-12-06 silk screen, other small changes
    [RAMBo.brd]
2012-12-06 tweak layout of smps
    [RAMBo.brd]
2012-12-06 add more decoupling caps, fix power layer dr err
    [RAMBo.brd]
2012-12-07 add decoupling to heater rails
    [RAMBo.brd]
2012-12-07 small heater polygon tweaks
    [RAMBo.brd]
2012-12-10 change fan1 mosfet to SOT23, add new fan
    [RAMBo.brd]
2012-12-10 Change license to same as Arduino
    The base of this board is derived from Arduino MEGA. Arduino requires
    that derivative hardware is published under the same license. Sorry for
    initially having it under GPL, my mistake.
2012-12-11 initial commint smart controller adapter
    untested
    [RAMBoSCadapter.brd, RAMBoSCadapter.sch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]
2012-12-13 fix reference designator and silk screen
    [RAMBo.brd]
2012-12-13 normalize connector values, fix silk screen
    [RAMBo.brd]
2013-01-01 rev1.1b, move output labels back to _tsilk layer,
    remove bstop boxes under mosfets and drivers to reduce chances of
    trapped chemicals after wave, add default values for new decoupling caps
    [RAMBo.brd]
2013-01-22 SCadapter silk changes
    [RAMBoSCadapter.brd, RAMBoSCadapter.sch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]
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2013-01-29 update documentation rev1.1b
    [RAMBoBOM.ods]
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2013-03-21 Adding PCB specifications, provided by johnnyr https://github.com/ultimachine/RAMBo/issues/5#issuecomment-15076545
2013-05-05 remove stop from JP3, update to eagle6.4
    [RAMBo.brd]
2013-05-05 change SMA package size
    [RAMBo.brd]
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2013-05-10 add freewheeling diodes, working on 32u2 layout,
    start adding icoupler
    [RAMBo.brd]
2013-05-13 finish icoupler addition, remove ps-select jumper
    [RAMBo.brd]
2013-05-16 rotate motor and serial ext for easier wave solder
    [RAMBo.brd]
2013-05-17 final connector move, change mount hole for wave
    fix drc and silk errors, misc fixes
    [RAMBo.brd]
2013-05-20 fix gnd fence
    [RAMBo.brd]
2013-06-03 change thieve style, rst-en trace added back,
    DTR resistor now pull up - now back to original usb reset behaviour of
    Rambo
    [RAMBo.brd]
2013-06-03 remove solder pads under mount holes
    [RAMBo.brd]
2013-06-10 rework psu layout, improve decoupling
    [RAMBo.brd]
2013-06-18 Add overvoltage protection to thermistor
    based on nophead, bobc, NoobMan, Cefiar, and STB's discussion at
    http://forums.reprap.org/read.php?13,197920,203564#msg-203564
    [RAMBo.brd]
2013-06-18 rework driver passives to make room for barcode
    removed resistor on reset/sleep
    [RAMBo.brd]
2013-06-18 Change bulk caps to PTH
    [RAMBo.brd]
2013-06-18 cleanup routing under 2560
    [RAMBo.brd]
2013-06-18 add 10uH to AVCC, better location/val decoupling
    for 2560, misc rerouting
    [RAMBo.brd]
2013-06-18 add UL and rohs silk instructions to document
    [RAMBo.brd]
2013-06-18 fix wire angle on supply layer, increment 1.2b
    [RAMBo.brd]
2013-06-18 remove random polygon on supply layer
    [RAMBo.brd]
2013-06-18 couple silk screen fixes
    [RAMBo.brd]
2013-06-25 Change SMPS source to mosfet input, diode on this
    rail to 27V zener
    [RAMBo.brd]
2013-06-28 set L2 part
    [RAMBo.brd]
2013-07-06 consolidate V-mot bulk caps to 1 470uF, move
    thermistor connectors, move PS-ON connector, add jumper to disable SMPS,
    adjust bulk cap placement on V-heat, misc layout and silk improvements
    [RAMBo.brd]
2013-07-09 fix pin number comments
2013-07-09 remove solder thieving, shrink through pads to
    improve wave, new stackup, fix some trace angles, more driver thermal
    improvements
    [RAMBo.brd]
2013-07-12 remove solder thieving, shrink through pads to
    improve wave, new stackup, fix some trace angles, improve stepper
    layout, silk screen fixes,
    [RAMBo.brd]
2013-07-16 move analog ext, layout changes, change vias
    around mosfets, silk screen fixes, change stack up,
    [RAMBo.brd]
2013-07-17 add a pin table
    [pin_list.ods]
2013-07-18 Change SMPS IC to LM22675, SMPS passives changed
    accordingly. Shorting SMPS jumper disables SMPS. Change reverse voltage
    diodes on low current rails.
    [RAMBo.brd]
2013-07-19 change SMPS to prefer 5V version of IC
    [RAMBo.brd]
2013-07-19 rerouting split planes and adjusting isolation
    [RAMBo.brd]
2013-07-19 move 1 via in HB heatsink
    [RAMBo.brd]
2013-07-19 straighten traces, add tplace to some components
    more polygon fixes
    [RAMBo.brd]
2013-08-20 Add Jordan's e2p adapter, reorganize folders
    [RAMBoSCadapter.brd, RAMBoSCadapter.sch, rambo_e2p.brd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]
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2013-08-23 fix thermal on bulk caps, minor reroute
    [RAMBo.brd]
2013-08-26 reroute n$15, remove mask between 2560 pads
    change stack up to match fab capabilities
    [RAMBo.brd]
2013-09-13 Clean up 1.2c Schematic
    [RAMBo.brd]
2013-09-30 shrink vias around motor drivers for wave proc
    [RAMBo.brd]
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2013-10-01 increment version to 1.2e
    [RAMBo.brd]
2013-10-05 pushing 1.2 docs
    [RAMBo.brd]
2013-10-30 Update BOM for 1.2
    [RAMBoBOM.ods]
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2013-11-08 shrink motor connector drill size
    [RAMBo.brd]
2013-11-08 Tweak A4982 footprint, cleanup schematic
    [RAMBo.brd]
2013-11-08 Fix MX2 and MX3 silk screen mix up
    [RAMBo.brd]
2013-11-08 Remove stop from vias in thermal planes
    [RAMBo.brd]
2013-11-10 update 0402 footprints
    [RAMBo.brd]
2013-11-10 update 0603 footprints
    [RAMBo.brd]
2013-11-10 update SOT669 footprint
    [RAMBo.brd, RAMBo.sch]
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2013-11-11 overprint paste on ATO fuseholder
    [RAMBo.brd, RAMBo.sch]
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2013-11-11 remove mask stops that were missed in f312f26
    [RAMBo.brd]
2013-11-11 fix some angles traces enter pads from 6e166ec
    also fixed C62, R13 silk overlap
    [RAMBo.brd]
2013-11-11 Clean up schematic, publish pdf in docs
    [RAMBo.sch]
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2013-11-22 change stepper test points to through hole
    YEN, ZDIR, and E0DIR moved to clear bottom traces
    [RAMBo.brd, RAMBo.sch]
2013-11-22 additional via to decoupling on motor supply
    cleanup traces
    [RAMBo.brd]
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2014-01-22 working on selective wave pallet layers
    [RAMBo.brd]
2014-01-22 Fix I2C schematic labels swapped
    [RAMBo.sch]
2014-02-03 Remove 2560 bootloader, get from arduino from Arduino
    To resolve https://github.com/ultimachine/RAMBo/issues/23 the bootloader
    should be pulled directly from the Arduino repository
    https://github.com/arduino/Arduino-stk500v2-bootloader
2014-02-17 add TVS diodes to motor outputs
    [RAMBo.brd, RAMBo.sch]
2014-02-17 Add Bi direction ESD Protection Diode
    USB shield ESD protection
    [RAMBo.brd, RAMBo.sch]
2014-02-17 Pull solder mask around QFN32 parts
    to reduce AOI false calls
    [RAMBo.brd, RAMBo.sch]
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2014-02-18 shrink 12.5mm capacitor drill size
    [RAMBo.brd, RAMBo.sch]
2014-02-19 fix silk screen 40d41b98ff
    [RAMBo.brd]
2014-03-06 remove via in D25 pad
    [RAMBo.brd]
2014-03-08 Change flyback diodes to SK310A
    [RAMBo.brd, RAMBo.sch]
2014-03-08 silk screen - fix a couple part names
    [RAMBo.brd]
2014-04-20 Add EMFIL pass through caps to motor outputs
    [RAMBo.brd, RAMBo.sch]
2014-04-21 Add ferrite beads to motor + htr/logic pwr input
    [RAMBo.brd, RAMBo.sch]
2014-04-21 Pull back copper and mask around fudicials
    [RAMBo.brd, RAMBo.sch]
2014-04-21 align vias, fix angle power plane
    [RAMBo.brd]
2014-04-22 Fix silks
    [RAMBo.brd]
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2014-08-19 Adding new User Manual documents for 1.1B boards. Manuals not yet approved by UltiMachine. Added .odt file, but opening it in LibreOffice doesn't seem to give the right formatting. Unfortunately, the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
2014-11-17 remove extra/false pin 1 mark on i2c
    [RAMBo.brd]
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2015-06-10 Update BOM docs to v1.3L
    [RAMBoBOM.ods]

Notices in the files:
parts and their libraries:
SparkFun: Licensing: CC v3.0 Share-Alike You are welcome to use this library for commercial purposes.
